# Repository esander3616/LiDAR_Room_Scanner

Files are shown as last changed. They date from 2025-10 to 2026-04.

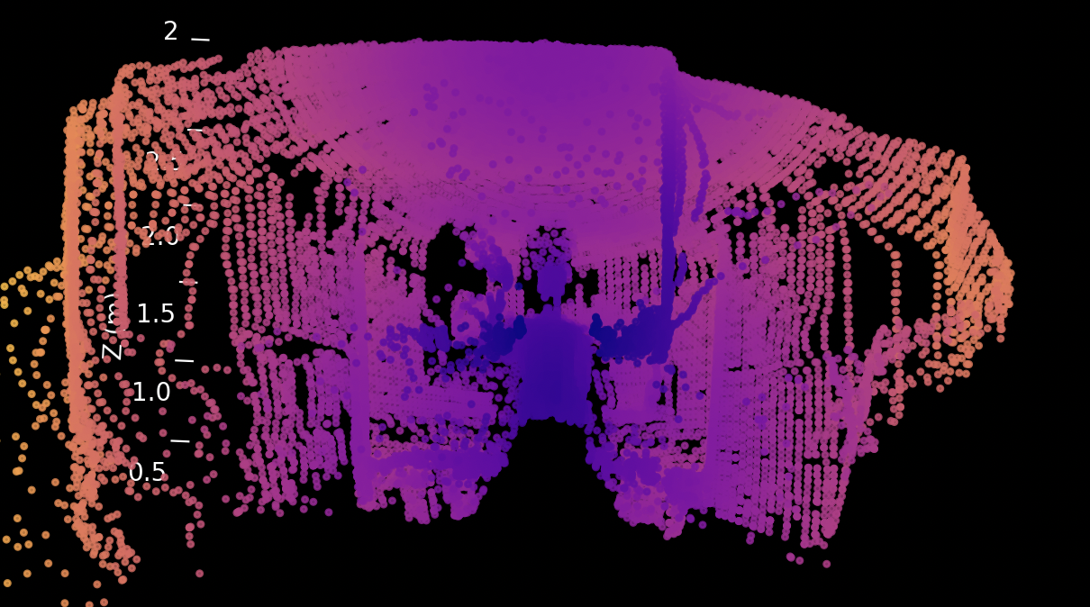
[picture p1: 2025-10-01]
printed_components+images/standing_person_scan.png

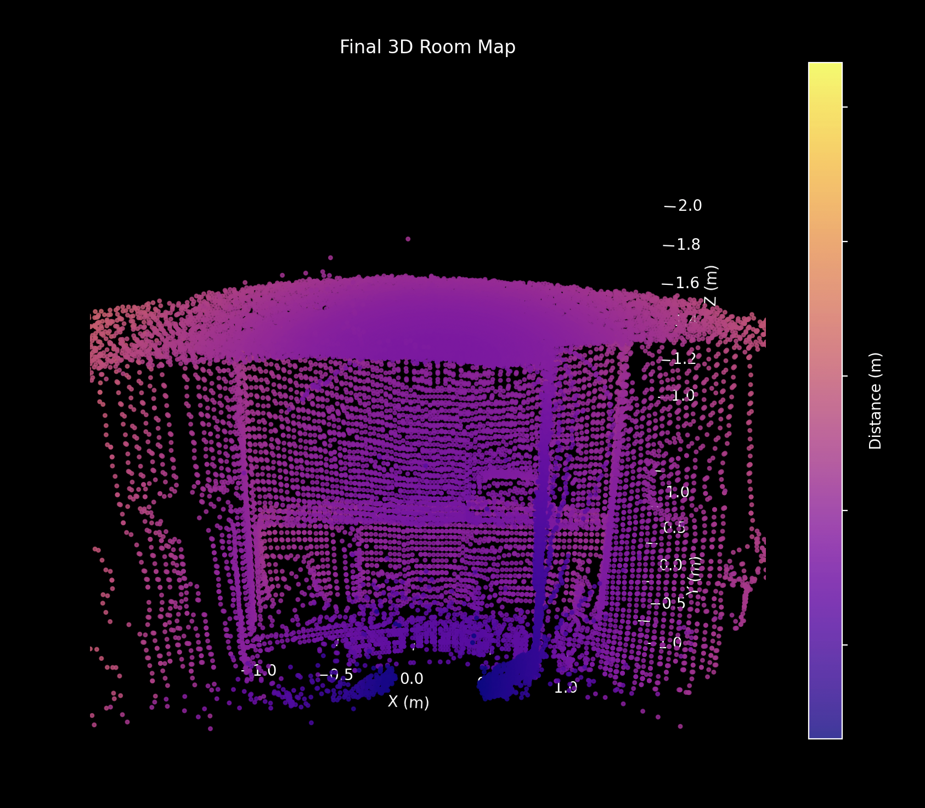
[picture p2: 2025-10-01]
printed_components+images/kitchen_scan.png

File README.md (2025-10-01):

# High-Speed 3D LiDAR Room Scanner

This repository contains the code for a 3D room scanner I built using an Arduino, a LiDAR sensor, and a couple of motors. The system rapidly captures distance and angle data to generate a 3D point cloud of a room, which is then visualized in real-time with a Python script.

The most interesting feature of this project is its high-speed scanning technique. Standard methods of stopping the scanner to take a reading at each point are quite slow. To solve this, I modified the servo to read its precise angle directly from its internal potentiometer while it moves at full speed. This approach allows the system to sample at over 500Hz, collecting over 28,000 data points and creating a detailed scan more than four times faster than comparable projects.

### Final Scan Result
kitchen_scan

## Software and Libraries

The project is split into two main parts: the Arduino firmware that runs the scanner, and the Python script that visualizes the data.

### Arduino (`arduino_scanner/scanner.ino`)
The firmware is written in C++ for the Arduino platform. You'll need to install the following libraries from the Arduino Library Manager:
* `Servo.h`: For controlling the servo motor.
* `AccelStepper.h`: For controlling the stepper motor's movement.
* `TFMPlus.h`: For communicating with the TFMini-S LiDAR sensor.

### Python (`visualizer.py`)
The real-time visualization is a Python script that reads the serial data from the Arduino and plots it. You'll need to install a few Python libraries to get it running.

You can install the dependencies by running this command in your terminal:
```bash 
pip install pyserial numpy matplotlib
```

## Hardware Assembly and Wiring
3D Print Parts: First, print the necessary housing and mounts. A stable mechanical assembly is key, as any wobbling can introduce errors in the final 3D model.

Modify the Servo: You'll need to carefully open the servo casing and solder a wire to the middle pin of the internal potentiometer. This wire will output an analog voltage corresponding to the servo's angle, allowing the server to sweep quickly while also getting accurate and fast readings.

Wire the Components:

TFMini-S LiDAR: Connect this to Serial2 on the Arduino.

Servo: Connect the main control pin to pin 6.

Stepper Motor: Connect IN1, IN2, IN3, IN4 to pins 8, 9, 10, 11.

Servo Potentiometer Wire: Connect the new wire you soldered to an analog pin, like A0.

## How to Run:
Upload the Code: Connect the Arduino to your computer and upload the scanner.ino sketch.

Open Serial Monitor: You can open the Arduino Serial Monitor at 115200 baud to see the raw r,phi,theta data being streamed.

Run the Visualizer: Execute the Python script from your terminal.

``` Bash
python visualizer.py
```
Scan: A 3D plot window will appear. The scanner will begin its 180-degree sweep, and points will be plotted in real-time.

Stop and Finalize: Once the scan is complete, press Ctrl+C in the terminal where the Python script is running. This will stop the live plotting and generate a final, high-quality plot of the complete point cloud.

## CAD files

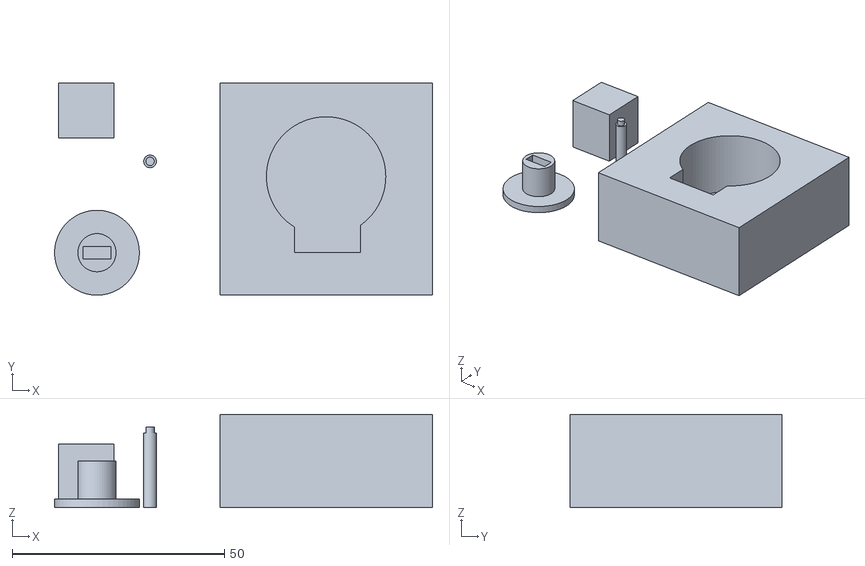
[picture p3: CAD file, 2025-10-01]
printed_components+images/SD7_3d_print/pan_tilt_parts.stl
89.0 x 50.0 x 22.0

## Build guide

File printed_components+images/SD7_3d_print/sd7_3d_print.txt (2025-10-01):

With the stepper motor attachment there was a cylinder attached to another smaller cylinder that was to be connected to the driving shaft of the motor. Additionally there was a concavity made with a prism that was added to the smaller cylinder to make a hole for the motor. Last operation was with the hole in the stepper motor holder. This was made with one rectangular prism and then taking away a cylinder and prism from the main prism. I received measurements of the motor from the online datasheet.

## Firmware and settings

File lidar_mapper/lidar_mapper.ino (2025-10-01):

#include <Servo.h>
#include <AccelStepper.h>
#include <TFMPlus.h>

// Pins
const int servoPin = 6;
const int potPin = A0;
const int IN1 = 8, IN2 = 9, IN3 = 10, IN4 = 11;

// Servo Config
Servo myServo;
const int servoMinWrite = 0;    // Servo 0 = -20 degrees relative
const int servoMaxWrite = 110;  // Servo 110 = 90 degrees relative
// these are relative to the xy plane in cartesian coordinates^

// Stepper Config
AccelStepper stepper(AccelStepper::HALF4WIRE, IN1, IN3, IN2, IN4);
const int stepsPerRev = 2048;
const int thetaStepDeg = 2;
const int stepperStepSize = (stepsPerRev * thetaStepDeg) / 360;

// Lidar Config
TFMPlus tfmP;
int16_t tfDist = 0;

// Pot Calibration
int rawPotMin = 0;
int rawPotMax = 1023;

// Function to calibrate potentiometer
void calibratePotentiometer() {
  myServo.write(servoMinWrite);
  delay(600);
  rawPotMin = analogRead(potPin);

  myServo.write(servoMaxWrite);
  delay(600);
  rawPotMax = analogRead(potPin);

  Serial.print("Pot calibration -> Min: ");
  Serial.print(rawPotMin);
  Serial.print(", Max: ");
  Serial.println(rawPotMax);
}

// Function to map potentiometer reading to phi degrees
float computePhiDeg(int rawPot) {
  float norm = (rawPot - rawPotMin) / float(rawPotMax - rawPotMin);
  norm = constrain(norm, 0.0, 1.0);
  float servoAngle = norm * (servoMaxWrite - servoMinWrite) + servoMinWrite;
  float phi = map(servoAngle, 0, 110, -20, 90); // Map to real-world degrees
  return phi;
}

// Function to configure the TFMini-S for 1000Hz frame rate
void configureLidar() {
  Serial2.begin(115200);
  tfmP.begin(&Serial2);
  delay(100);

  tfmP.sendCommand(SOFT_RESET, 0);
  delay(500);
  tfmP.sendCommand(SET_SERIAL_MODE, 0);
  delay(100);
  tfmP.sendCommand(SAVE_SETTINGS, 0);
  delay(100);
  tfmP.sendCommand(SET_FRAME_RATE, 1000); // 1000Hz
  delay(100);
}

// Sweep servo down, sample pot and lidar at high rate
void sweepDownAndUp(int direction) {
  int targetAngle = (direction > 0) ? servoMaxWrite : servoMinWrite;
  myServo.write(targetAngle);
  delay(300); // Let it start moving

  unsigned long lastSampleTime = 0;
  const unsigned int sampleInterval = 2; // 500Hz sampling (~2ms)

  while (true) {
    unsigned long now = millis();
    if (now - lastSampleTime >= sampleInterval) {
      lastSampleTime = now;
      int rawPot = analogRead(potPin);
      float phiDeg = computePhiDeg(rawPot);

      if (tfmP.getData(tfDist)) {
        float r = tfDist / 100.0;
        float thetaDeg = (360.0 * stepper.currentPosition()) / stepsPerRev / 2.0; // Half scan
        Serial.print("r:");
        Serial.print(r, 2);
        Serial.print(",phi:");
        Serial.print(phiDeg);
        Serial.print(",theta:");
        Serial.println(thetaDeg);
      }
    }

    // Checking condition to see if the servo has finished moving
    int currentServo = map(analogRead(potPin), rawPotMin, rawPotMax, servoMinWrite, servoMaxWrite);
    currentServo = constrain(currentServo, servoMinWrite, servoMaxWrite);

    if (direction > 0 && currentServo >= servoMaxWrite - 2) break;
    if (direction < 0 && currentServo <= servoMinWrite + 2) break;
  }

  delay(300); // Ensure full reach
}

void setup() {
  Serial.begin(115200);
  delay(100);

  myServo.attach(servoPin);
  stepper.setMaxSpeed(1000);
  stepper.setAcceleration(500);

  configureLidar();

  calibratePotentiometer();

  stepper.setCurrentPosition(0);
}

void loop() {
  for (int currentThetaStep = 0; currentThetaStep < stepsPerRev; currentThetaStep += stepperStepSize) {
    stepper.moveTo(currentThetaStep);
    stepper.runToPosition();

    sweepDownAndUp(-1); // Sweep down
    sweepDownAndUp(1);  // Sweep up
  }

  Serial.println("Scan complete.");
  stepper.moveTo(0);
  stepper.runToPosition();

  while (true); // Halt
}

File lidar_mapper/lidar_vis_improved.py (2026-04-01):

import serial
import numpy as np
import matplotlib.pyplot as plt
from mpl_toolkits.mplot3d import Axes3D

# Serial port settings
PORT = '/dev/cu.usbmodem1301'
BAUD = 115200

UPDATE_EVERY = 20  # Update plot every 20 points

def spherical_to_cartesian(r, theta_deg, phi_deg):
    theta = np.radians(theta_deg)
    phi = np.radians(phi_deg)
    x = r * np.cos(phi) * np.cos(theta)
    y = r * np.cos(phi) * np.sin(theta)
    z = r * np.sin(phi)
    return x, y, z

def main():
    ser = serial.Serial(PORT, BAUD, timeout=1)
    print(f"Connected to {PORT} at {BAUD} baud.")

    x_vals, y_vals, z_vals, r_vals = [], [], [], []

    plt.ion()
    fig = plt.figure(figsize=(10, 8))
    ax = fig.add_subplot(111, projection='3d')

    fig.patch.set_facecolor('black')
    ax.set_facecolor('black')
    ax.grid(False)
    ax.w_xaxis.pane.set_color((0, 0, 0, 0))
    ax.w_yaxis.pane.set_color((0, 0, 0, 0))
    ax.w_zaxis.pane.set_color((0, 0, 0, 0))
    ax.tick_params(colors='white')
    ax.set_xlabel('X (m)', color='white')
    ax.set_ylabel('Y (m)', color='white')
    ax.set_zlabel('Z (m)', color='white')
    ax.set_xlim(-3, 3)
    ax.set_ylim(-3, 3)
    ax.set_zlim(0, 3)
    ax.set_title('3D Room Mapping Observatory View', color='white')

    # initilized scatter
    scatter = ax.scatter([], [], [], c=[], cmap='plasma', s=5, alpha=0.8)
    colorbar = fig.colorbar(scatter, ax=ax, label='Distance (m)')
    colorbar.ax.yaxis.set_tick_params(color='white')
    colorbar.ax.yaxis.label.set_color('white')
    colorbar.outline.set_edgecolor('white')

    counter = 0

    try:
        while True:
            line = ser.readline().decode('utf-8').strip()
            if line.startswith("r:"):
                try:
                    parts = line.split(',')
                    r = float(parts[0].split(':')[1])
                    theta = float(parts[2].split(':')[1])
                    phi = float(parts[1].split(':')[1])
                    x, y, z = spherical_to_cartesian(r, theta, phi)

                    x_vals.append(x)
                    y_vals.append(y)
                    z_vals.append(z)
                    r_vals.append(r)

                    counter += 1
                    if counter % UPDATE_EVERY == 0:
                        scatter._offsets3d = (x_vals, y_vals, z_vals)
                        scatter.set_array(np.array(r_vals))
                        plt.pause(0.001)

                except Exception as e:
                    print("Parse error:", e)

    except KeyboardInterrupt:
        print("Stopping.")
        ser.close()
        plt.ioff()
        
        fig = plt.figure(figsize=(10, 8))
        ax = fig.add_subplot(111, projection='3d')
        fig.patch.set_facecolor('black')
        ax.set_facecolor('black')
        ax.grid(False)
        ax.w_xaxis.pane.set_color((0, 0, 0, 0))
        ax.w_yaxis.pane.set_color((0, 0, 0, 0))
        ax.w_zaxis.pane.set_color((0, 0, 0, 0))
        ax.tick_params(colors='white')
        ax.set_xlabel('X (m)', color='white')
        ax.set_ylabel('Y (m)', color='white')
        ax.set_zlabel('Z (m)', color='white')
        ax.set_xlim(-3, 3)
        ax.set_ylim(-3, 3)
        ax.set_zlim(0, 3)
        ax.set_title('Final 3D Room Map', color='white')

        scatter = ax.scatter(x_vals, y_vals, z_vals, c=r_vals, cmap='plasma', s=5, alpha=0.8)
        colorbar = fig.colorbar(scatter, ax=ax, label='Distance (m)')
        colorbar.ax.yaxis.set_tick_params(color='white')
        colorbar.ax.yaxis.label.set_color('white')
        colorbar.outline.set_edgecolor('white')

        plt.show()

if __name__ == "__main__":
    main()
